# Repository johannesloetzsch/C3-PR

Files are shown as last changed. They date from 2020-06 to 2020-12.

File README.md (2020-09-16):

# C3 Presence Robot
A simple and affordable telepresence experimentation platform. Based on the [Espressives ESP32-CAM example revisited](https://github.com/easytarget/esp32-cam-webserver) which in itself is a rework of the ['official' ESP32 Camera example sketch](https://github.com/espressif/arduino-esp32/tree/master/libraries/ESP32/examples/Camera/CameraWebServer) from Espressif.

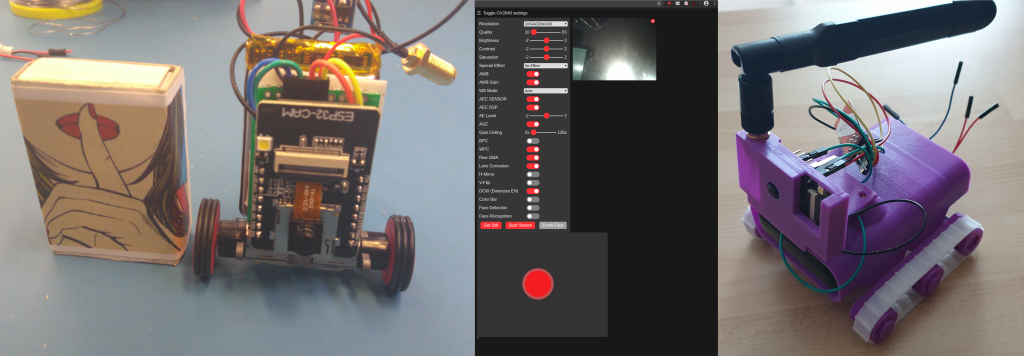
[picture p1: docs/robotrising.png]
Robots rising


Construction Howto in German: https://codimd.c3d2.de/c3-pr-tutorial

#### AI-THINKER ESP32-CAM vs Other Modules:

The current design uses the [AI-THINKER ESP32-CAM](https://github.com/raphaelbs/esp32-cam-ai-thinker/blob/master/assets/ESP32-CAM_Product_Specification.pdf) boards. If possible we will keep compatibilty with other modules. 

* For some other good examples and information on ESP32 based webcams I also recommend the sketches here:
https://github.com/raphaelbs/esp32-cam-ai-thinker

* The AI thinker wiki can be quite informative, when run through an online translator and read sensibly:
https://wiki.ai-thinker.com/esp32-cam

#### Motor Driver Hardware

Development of a small motor driver clip-on board is under way. If you want to get started now, wire your own [Dual TB6612FNG](https://www.sparkfun.com/products/14451) motor driver board in a way that AIN2 (BIN2) is the inverted signal of AIN1 (BIN1). We only have so many GPIOs, so we need to use them wisely.

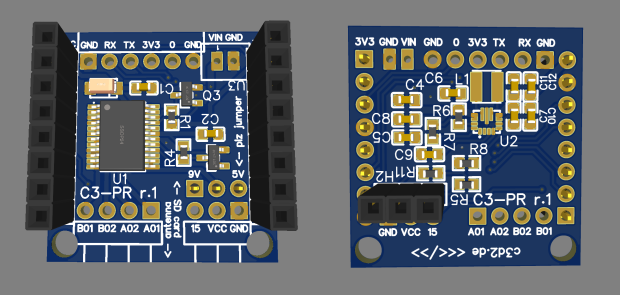
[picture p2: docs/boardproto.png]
board prototype

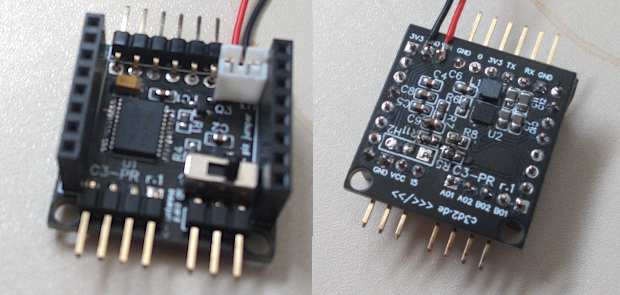
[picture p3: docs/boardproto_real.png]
board prototype


See pcb folder for more information on shematics and gerber files.

* A usefull guide to the ESP32-CAM GPIOs is https://randomnerdtutorials.com/esp32-cam-ai-thinker-pinout/

#### Mechanical Parts

Various designs for mechanical parts are under development.

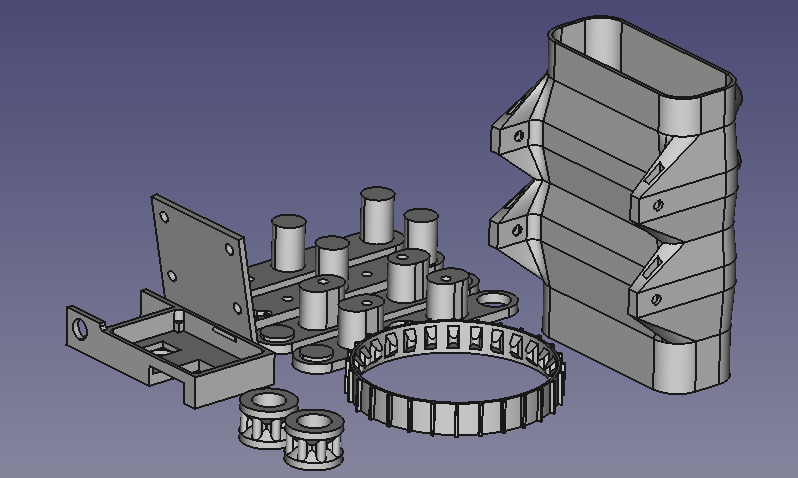
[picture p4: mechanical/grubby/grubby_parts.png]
grubby style design


## Troubleshooting:

Please read this excellent guide for help with common issues of the ESP32-CAM module:
https://randomnerdtutorials.com/esp32-cam-troubleshooting-guide/

## Setup:

* For programming you will need a suitable development environment. We had a lot of fun and 'fun' with the Arduino IDE, but PlatformIO leaves it in the dust. Just check out this repo, set your wifi credentials according to `myconfig.sample.h` and you should be good. However if want to use the Arduino IDE, rename `esp32-cam-webserver.cpp` to `esp32-cam-webserver.ino` in the `src` directory. The Arduino IDE might still work for you. For further instructions and wiring, please refer to the [original repo](https://github.com/easytarget/esp32-cam-webserver).

## Notes: 
* This currently ONLY gets tested with the AI-THINKER modules with OV2640 camera installed. We try to keep the code for other cameras in but this might change in the future.

## Plans
* Improve Wifi, add a captive portal (e.g. [AutoConnect](https://github.com/Hieromon/AutoConnect) for setup.
* Over the air updates.
* Improve motor control and UI, all this is currently very very basic.
* Concurrent access to website and stream doesn't seem to work well (or at all). Fix this.

## References
How to use gamepads in browsers (no external libraries needed, BROWSER DEPENDENT!)
https://gamedevelopment.tutsplus.com/de/tutorials/using-the-html5-gamepad-api-to-add-controller-support-to-browser-games--cms-21345
Differential Steering with Gamepads
https://www.impulseadventure.com/elec/robot-differential-steering.html

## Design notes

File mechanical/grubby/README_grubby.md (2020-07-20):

### Parts for Grubby Design

It looks like a mole but it's a grubby!

Designed aroud a 10Ah jonkuu power bank [amazon link](https://www.amazon.de/gp/product/B07Y1TCDT1).

The threads must be printed in flexible material. TPE prints just fine.

You will need M3x20mm Screws, M3 square nuts and for mountimg the camera holder some heatset inserts.

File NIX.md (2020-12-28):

This directory contains a `configuration.nix`.
It can be used to create a **livestick** containing everything needed for:
- programming the firmware with `platformio`
- running `c3pr-proxy` (systemd-unit)
- running `c3pr-ui` (systemd-unit)

For installation:
- use this repo as `/mnt/etc/nixos`
- adjust device names in `hardware-configuration-livestick.nix` (`boot.loader.grub.device` and `fileSystems`)
- run `nixos-install`

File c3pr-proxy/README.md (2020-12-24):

# C3 Presence Robot Proxy
Plug-in to the [mitmproxy](https://mitmproxy.org) for the management of C3PR. The code was written from friday to sonday late morning of [Datenspuren 2020](https://datenspuren.de/2020).

## Functions

The proxy stores a mapping from sessions to roboters. If an incoming client is not found in the mapping table, an overview page is shown. The overview page allows users to pick free roboters.

If a mapping for an incoming request is found in the mapping table, it is forwarded to the robot.

## Usage

1. Download the mitmproxy binary package.
2. Start application with command line:
   mitmproxy --mode reverse:http://ignored.example.com -s c3pr-selector.py --set block_global=false
3. Switch to event log for debugging:
   `Shift + 'e'` ('E')

## TODOS

- Send motor stop on time-out
- Cancel reservation on errors

Have fun, [norbert](https://wiki.c3d2.de/Benutzer:Norbert)

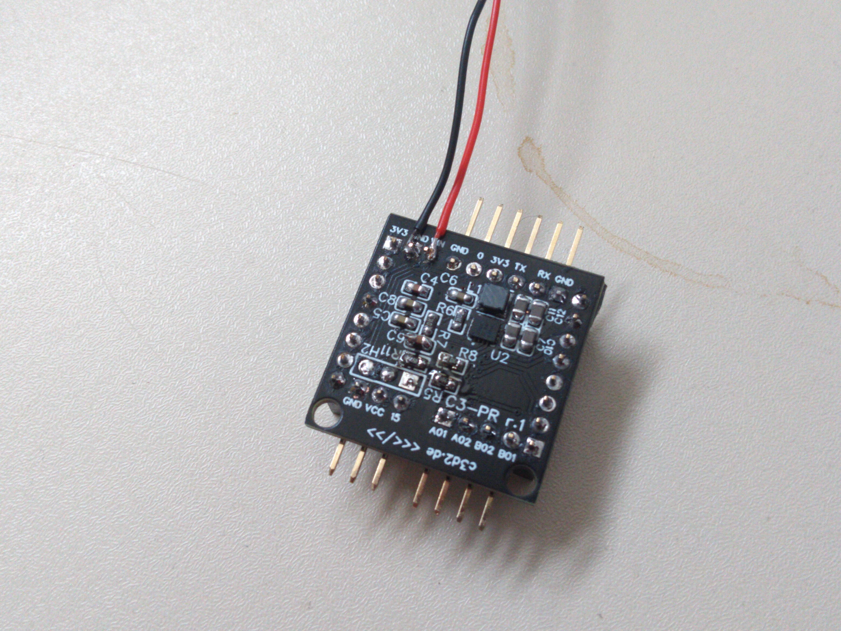
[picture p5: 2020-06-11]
pcb/v1/images/back.jpg

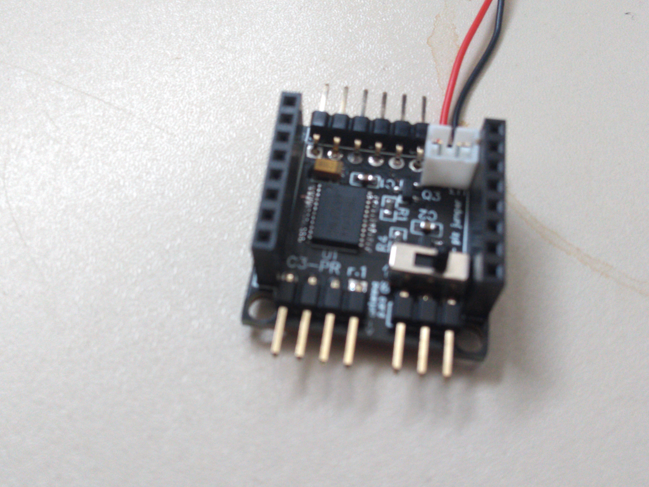
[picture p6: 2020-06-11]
pcb/v1/images/front.jpg

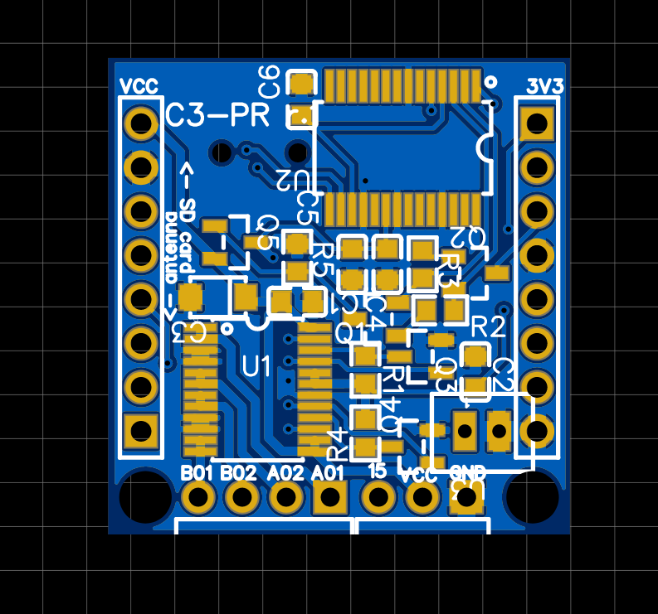
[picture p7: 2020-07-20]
pcb/v2-ftdi/images/front.png

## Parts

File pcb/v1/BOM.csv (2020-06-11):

ID | Name | Designator | Footprint | Quantity | Manufacturer Part | Manufacturer | Supplier | Supplier Part | LCSC Assembly
1 | 10uF | C3 | CAP-SMD_L3.2-W1.6 | 1 | CA45-A016K106T | Xiangyee | LCSC | C119051 | Yes
2 | 220S-1*8P H=8.5MM Ytype Gold-plated | H3,H4 | HDR-TH_8P-P2.54-V | 2 | 220S-1*8P H=8.5MM Ytype Gold-plated | Ckmtw | LCSC | C124416
3 | 68.1K | R8 | R0603 | 1 | RMC060368.1K1%N | Tyohm | LCSC | C269505
4 | 680K | R5 | R0603 | 1 | RK73B1JTTD684J | KOA Speer Elec | LCSC | C276114
5 | 22uF | C10,C11,C12 | C0603 | 3 | GRM188B30J226MEA0D | MuRata | LCSC | C15500
6 | 210R-1*6PCurved needle Reverse bending Gold-plated black | H6 | HDR-TH_6P-P2.54-H-W10.3 | 1 | 210R-1*6PCurved needle Reverse bending Gold-plated black | Ckmtw | LCSC | C124367
7 | 100nF | C8,C9 | C0603 | 2 | CC0603JRX7R9BB104 | YAGEO | LCSC | C91183
8 | A2541WV-3P | H2 | HDR-TH_3P-P2.54-V_A2541HWV-3P | 1 | A2541WV-3P | Changjiang Connectors | LCSC | C225478
9 | 10uF | C4,C5,C6,C7 | C0603 | 4 | GRM188B30J106KE47D | Murata Electronics | LCSC | C393030
10 | TPS630701RNMT | U2 | VQFN-15_L3.0-W2.5-P0.50-BL | 1 | TPS630701RNMT | TI | LCSC | C181473
11 | 10K | R1,R4,R6,R7 | R0603 | 4 | RMC060310K1%N | Tyohm | LCSC | C269701
12 | JST-PH_2-PIN_HEADER | U3 | JST_B2B-PH_HEADER | 1
13 | MTB125-1103R1 | H1 | HDR-TH_3P-P2.54-H-W10.0 | 1 | MTB125-1103R1 | MINTRON | LCSC | C376121
14 | BSS123_C397175 | Q3,Q4 | SOT-23_L2.9-W1.3-P0.95-LS2.4-BR | 2 | BSS123 | AnBon | LCSC | C397175 | Yes
15 | TB6612FNG,C,8,EL | U1 | SSOP-24_L8.1-W5.3-P0.65-LS7.8-BL | 1 | TB6612FNG,C,8,EL | TOSHIBA | LCSC | C141517 | Yes
16 | 100nF | C1,C2 | C0603 | 2 | 0603B104K500AT | Guangdong Fenghua Advanced Tech | LCSC | C191538
17 | 1.5uH | L1 | IND-SMD_L3.0-W3.0_SMNR3015 | 1 | SMNR3015-1R5MT | SXN | LCSC | C135238
18 | A2541WR-4P | H5 | HDR-TH_4P-P2.54-H-W10.3 | 1 | A2541WR-4P | Changjiang Connectors | LCSC | C225490
19 | 365K | R11 | R0603 | 1 | RCT03365KFLF | Hong Kong Resistors | LCSC | C178113

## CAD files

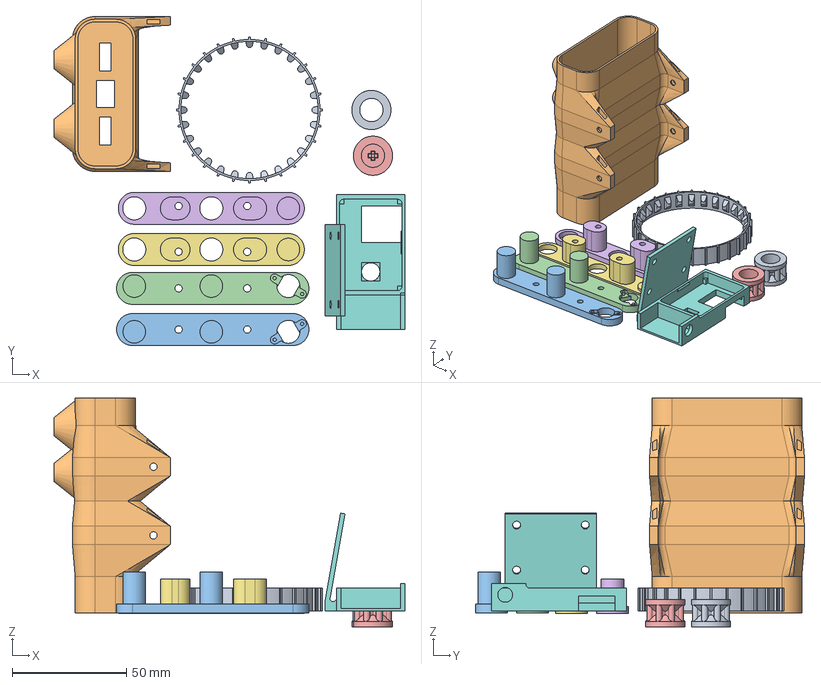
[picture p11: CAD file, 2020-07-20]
mechanical/grubby/RobotParts.FCStd
153.5 x 143.9 x 100.0 mm
Thread_printable
MainBody_printable
LeftDriveSkid_printable
RightDriveSkid_printable
DriveGear_printable
RightDriveGearRetainer_printable
LeftDriveGearRetainer_printable
EspCamHousing_printable
IdlerGear_printable

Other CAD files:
mechanical/grubby/RobotParts.amf
mechanical/grubby/RobotParts.stl

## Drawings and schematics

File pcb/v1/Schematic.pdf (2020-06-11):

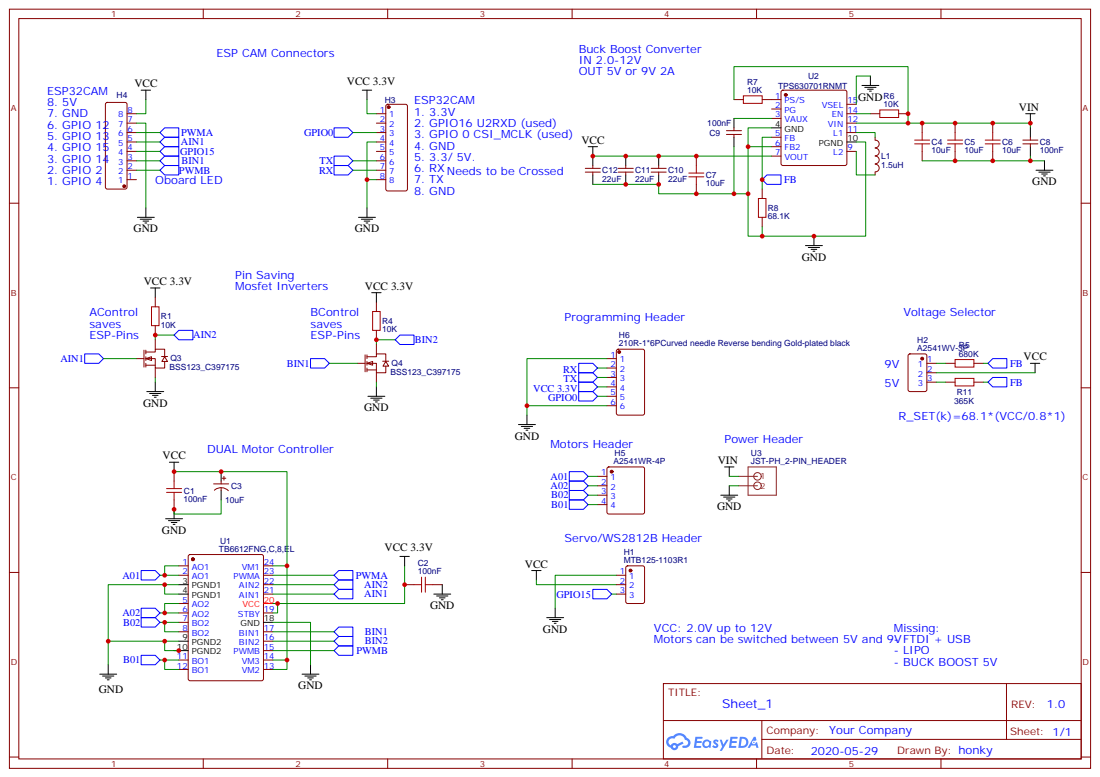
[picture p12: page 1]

PGND 10 L1 11 VIN 12 EN 14 VSEL 15

VCC: 2.0V up to 12V
Motors can be switched between 5V and 9V

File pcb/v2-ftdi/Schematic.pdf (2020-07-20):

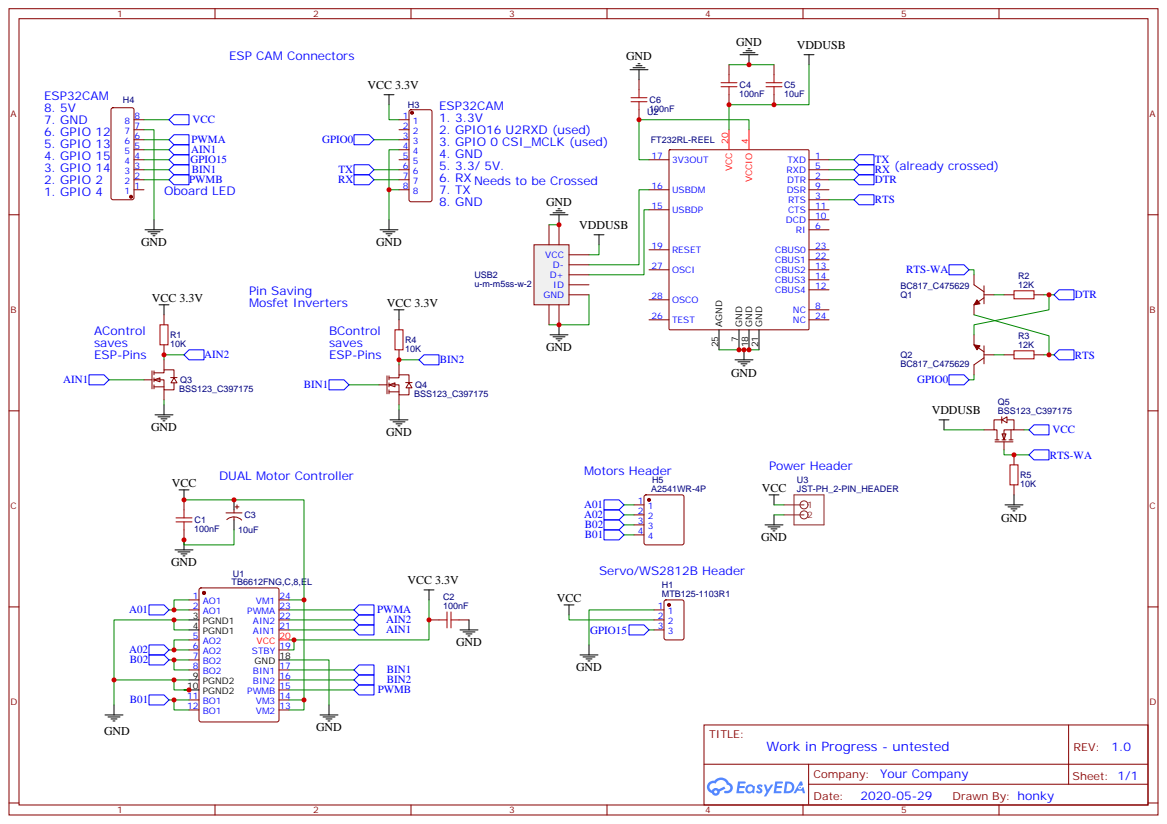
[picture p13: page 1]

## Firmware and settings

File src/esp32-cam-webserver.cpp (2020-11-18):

#include "esp_camera.h"
#include <esp_wifi.h>
#include "robot_pins.h"
#include <WiFi.h>

/* This sketch is a extension/expansion/reork of the 'official' ESP32 Camera example
 *  sketch from Expressif:
 *  https://github.com/espressif/arduino-esp32/tree/master/libraries/ESP32/examples/Camera/CameraWebServer
 *  
 *  It is modified to allow control of Illumination LED Lamps's (present on some modules),
 *  greater feedback via a status LED, and the HTML contents are present in plain text
 *  for easy modification. 
 *  
 *  A camera name can now be configured, and wifi details can be stored in an optional 
 *  header file to allow easier updated of the repo.
 *  
 *  The web UI has had minor changes to add the lamp control when present, I have made the 
 *  'Start Stream' controls more accessible, and add feedback of the camera name/firmware.
 *  
 *  
 * note: Make sure that you have either selected ESP32 AI Thinker,
 *       or another board which has PSRAM enabled to use high resolution camera modes
*/

// Select camera board model
//#define CAMERA_MODEL_WROVER_KIT
//#define CAMERA_MODEL_ESP_EYE
//#define CAMERA_MODEL_M5STACK_PSRAM
//#define CAMERA_MODEL_M5STACK_WIDE
//#define CAMERA_MODEL_M5STACK_NO_PSRAM
#define CAMERA_MODEL_AI_THINKER

// Select camera module used on the board
#define CAMERA_MODULE_OV2640
//#define CAMERA_MODULE_OV3660

#if __has_include("myconfig.h")
  // I keep my settings in a seperate header file
  // pls copy the sample file and place it in src folder
  #include "myconfig.h"
#else
  const char* ssid = "ZW public";
  const char* password =  "";
#endif

// A Name for the Camera. (can be set in myconfig.h)
#ifdef CAM_NAME
  char myName[] = CAM_NAME;
#else
  char myName[] = "C3PR-uninitialised";
#endif

// This will be displayed to identify the firmware
char myVer[] PROGMEM = __DATE__ " @ " __TIME__;

#include "camera_pins.h"

// Status and illumination LED's
#ifdef LAMP_PIN 
  int lampVal = 0; // Current Lamp value, range 0-100, Start off
#else 
  int lampVal = -1; // disable Lamp
#endif         
int lampChannel = 7;     // a free PWM channel (some channels used by camera)
                        // according to https://esp32.com/viewtopic.php?t=11379 those are channel 1 and 2
const int pwmfreq = 50000;     // 50K pwm frequency
const int pwmresolution = 9;   // duty cycle bit range
// https://diarmuid.ie/blog/pwm-exponential-led-fading-on-arduino-or-other-platforms
const int pwmIntervals = 100;  // The number of Steps between the output being on and off
float lampR;                   // The R value in the PWM graph equation (calculated in setup)


void startCameraServer();
void flashLED(int flashtime);

void setup() {
  Serial.begin(115200);
  Serial.setDebugOutput(true);
  Serial.println();
  Serial.println("====");
  Serial.print("esp32-cam-webserver: ");
  Serial.println(myName);
  Serial.print("Code Built: ");
  Serial.println(myVer);

// If we have a notification LED set it to output
#ifdef LED_PIN
    pinMode(LED_PIN, OUTPUT);
    digitalWrite(LED_PIN, LED_OFF); 
#endif

#ifdef LAMP_PIN
  ledcSetup(lampChannel, pwmfreq, pwmresolution); // configure LED PWM channel
  ledcWrite(lampChannel, lampVal);                // set initial value
  ledcAttachPin(LAMP_PIN, lampChannel);           // attach the GPIO pin to the channel 
  // Calculate the PWM scaling R factor: 
  // https://diarmuid.ie/blog/pwm-exponential-led-fading-on-arduino-or-other-platforms
  lampR = (pwmIntervals * log10(2))/(log10(pow(2,pwmresolution)));
#endif

  camera_config_t config;
  config.ledc_channel = LEDC_CHANNEL_0;
  config.ledc_timer = LEDC_TIMER_0;
  config.pin_d0 = Y2_GPIO_NUM;
  config.pin_d1 = Y3_GPIO_NUM;
  config.pin_d2 = Y4_GPIO_NUM;
  config.pin_d3 = Y5_GPIO_NUM;
  config.pin_d4 = Y6_GPIO_NUM;
  config.pin_d5 = Y7_GPIO_NUM;
  config.pin_d6 = Y8_GPIO_NUM;
  config.pin_d7 = Y9_GPIO_NUM;
  config.pin_xclk = XCLK_GPIO_NUM;
  config.pin_pclk = PCLK_GPIO_NUM;
  config.pin_vsync = VSYNC_GPIO_NUM;
  config.pin_href = HREF_GPIO_NUM;
  config.pin_sscb_sda = SIOD_GPIO_NUM;
  config.pin_sscb_scl = SIOC_GPIO_NUM;
  config.pin_pwdn = PWDN_GPIO_NUM;
  config.pin_reset = RESET_GPIO_NUM;
  config.xclk_freq_hz = 20000000;
  config.pixel_format = PIXFORMAT_JPEG;
  //init with high specs to pre-allocate larger buffers
  if(psramFound()){
    config.frame_size = FRAMESIZE_UXGA;
    config.jpeg_quality = 10;
    config.fb_count = 2;
  } else {
    config.frame_size = FRAMESIZE_SVGA;
    config.jpeg_quality = 12;
    config.fb_count = 1;
  }

#if defined(CAMERA_MODEL_ESP_EYE)
  pinMode(13, INPUT_PULLUP);
  pinMode(14, INPUT_PULLUP);
#endif

  // camera init
  esp_err_t err = esp_camera_init(&config);
  if (err != ESP_OK) {
    Serial.printf("Camera init failed with error 0x%x", err);
    return;
  }

  sensor_t * s = esp_camera_sensor_get();
  //initial sensors are flipped vertically and colors are a bit saturated
  if (s->id.PID == OV3660_PID) {
    s->set_vflip(s, 1);       //flip it back
    s->set_brightness(s, 1);  //up the brightness just a bit
    s->set_saturation(s, -2); //lower the saturation
  }
  //drop down frame size for higher initial frame rate
  s->set_framesize(s, FRAMESIZE_VGA);

#if defined(CAMERA_MODEL_M5STACK_WIDE)
  s->set_vflip(s, 1);
  s->set_hmirror(s, 1);
#endif

  // Mötör init
  pinMode(MOTOR_L_PWM_PIN, OUTPUT);
  ledcSetup(MOTOR_L_PWM_CHAN, MOTOR_PWM_FREQ_HZ, MOTOR_PWM_RES_BIT);
  ledcAttachPin(MOTOR_L_PWM_PIN, MOTOR_L_PWM_CHAN);
  ledcWrite(MOTOR_L_PWM_CHAN, 0); //off
  pinMode(MOTOR_R_PWM_PIN, OUTPUT);
  ledcSetup(MOTOR_R_PWM_CHAN, MOTOR_PWM_FREQ_HZ, MOTOR_PWM_RES_BIT);
  ledcAttachPin(MOTOR_R_PWM_PIN, MOTOR_R_PWM_CHAN);
  ledcWrite(MOTOR_R_PWM_CHAN, 0); //off
  pinMode(MOTOR_L_DIR_PIN, OUTPUT);
  digitalWrite(MOTOR_L_DIR_PIN, LOW); 
  pinMode(MOTOR_R_DIR_PIN, OUTPUT);
  digitalWrite(MOTOR_R_DIR_PIN, LOW); 

  // Feedback that hardware init is complete and we are now attempting to connect
  Serial.println("");
  Serial.print("Connecting to Wifi network: ");
  Serial.println(ssid);
  flashLED(400);
  delay(100);

  WiFi.begin(ssid, password);

  while (WiFi.status() != WL_CONNECTED) {
    delay(250);  // Wait for Wifi to connect. If this fails wifi the code basically hangs here.
                 // - It would be good to do something else here as a future enhancement.
                 //   (eg: go to a captive AP config portal to configure the wifi)
  }

  // feedback that we are connected
  Serial.println("WiFi connected");
  Serial.println("");
  flashLED(200);
  delay(100);
  flashLED(200);
  delay(100);
  flashLED(200);

  // Start the Stream server, and the handler processes for the Web UI.
  startCameraServer();

  Serial.print("Camera Ready!  Use 'http://");
  Serial.print(WiFi.localIP());
  Serial.println("' to connect");
}

// Notification LED 
void flashLED(int flashtime)
{
#ifdef LED_PIN                    // If we have it; flash it.
  digitalWrite(LED_PIN, LED_ON);  // On at full power.
  delay(flashtime);               // delay
  digitalWrite(LED_PIN, LED_OFF); // turn Off
#else
  return;                         // No notifcation LED, do nothing, no delay
#endif
} 


void loop() {
  flashLED(200); //blink led as heartbeat
  // Just loop forever.
  // The stream and URI handler processes initiated by the startCameraServer() call at the
  // end of setup() will handle the camera and UI processing from now on.
  delay(5000);
}

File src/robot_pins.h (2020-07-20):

// Pin and PWM definitions for robot peripherals (actuators, LEDs, ...)

// TB6612FNG with 
// GPIO 12 - PWM A left motor
// GPIO 13 - PWM B right motor
// GPIO 14 - DIR A 
// GPIO 15 - DIR B

#define MOTOR_L_PWM_PIN  12
#define MOTOR_R_PWM_PIN  2
#define MOTOR_L_DIR_PIN  13
#define MOTOR_R_DIR_PIN  14

#define MOTOR_L_PWM_CHAN 3
#define MOTOR_R_PWM_CHAN 4
// PWM resolution
#define MOTOR_PWM_RES_BIT 10
// PWM frequency
#define MOTOR_PWM_FREQ_HZ 10000

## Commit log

2020-06-02 Externalize motor pin definitions
2020-06-02 Reduce the initial frame size to VGA 640x480
2020-06-05 provide PWM control for motors
2020-06-11 pcb v1 added
    [BOM.csv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]
2020-06-19 add 3d print parts for grubby design
    [RobotParts.FCStd, RobotParts.amf, RobotParts.stl]
2020-07-20 adjusted pins to current board, added heartbeat
2020-07-20 added single sided ftdi pcb
    [Gerber_BoardOutline.GKO, Gerber_BottomLayer.GBL, Gerber_BottomPasteMaskLayer.GBP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]
2020-12-30 ui: buttons
2021-01-29 use button to control robot
2021-02-04 fixed buttons when stream is rotated
2021-02-19 counterbalance steering bias
